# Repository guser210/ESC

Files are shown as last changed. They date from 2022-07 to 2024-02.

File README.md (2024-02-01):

# ESC

#ESC V2
https://github.com/guser210/ESC-V2

ESC - Electronic Speed Controller for BLDC Motors.

You can find more information on this link,
https://discord.gg/pByahDupYP

Component list: 

STM32G0 ARM Processor: Qty 1
https://www.mouser.com/ProductDetail/511-STM32G070KBT6

ADP Gate Driver: Qty 3
https://www.mouser.com/ProductDetail/863-ADP3120AJRZ-RL

Comparator: Qty 1
https://www.mouser.com/ProductDetail/511-LM339P

10v Regulator: Qty 1
https://www.mouser.com/ProductDetail/595-UA78L10ACLPRE3

3.3v Regulator: Qty 1
https://www.mouser.com/ProductDetail/595-LP2950-33LPRE3

Toshiba 30v 320A mosfet: Qty 6
https://www.mouser.com/ProductDetail/757-TPHR9203PL1LQ

1000uF Cap 100v: Qty 1
https://www.mouser.com/ProductDetail/80-ESK108M050AL4AA

4.7uF 100v ceramic capacitor: Qty 6
https://www.mouser.com/ProductDetail/81-GRM31CC72A475KE1K

1uf 100v ceramic capacitor: Qty 3
https://www.mouser.com/ProductDetail/963-HMR212CC7105KG-T

0.1uf 250v ceramic capacitor: Qty 1
https://www.mouser.com/ProductDetail/810-C2012X7T2E104MST

Switching diode 400v 3A: Qty 3
https://www.mouser.com/ProductDetail/241-GS1004FLR100001

Breakout boards:

LQFP-32 for ARM Processor: Qty 1
https://oshpark.com/shared_projects/X7qWhbM5

Mosfet driver: Qty 3
https://oshpark.com/shared_projects/A9uEdszS

Comparator LM339-TSSOP-14: Qty 1
https://oshpark.com/shared_projects/zJzdy7s3

Mosfet: Qty 3
https://oshpark.com/shared_projects/zwIIKerc

Flight Controller: Qty 1 Optional
https://www.getfpv.com/lumenier-lux-f7-ultimate-flight-controller-dual-gyros.html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 

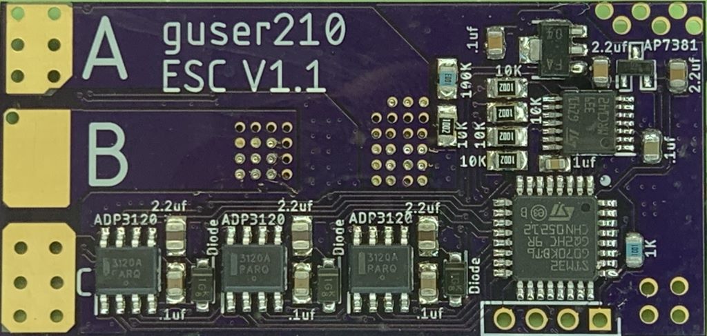
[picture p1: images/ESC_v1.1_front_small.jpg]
PCB Front test


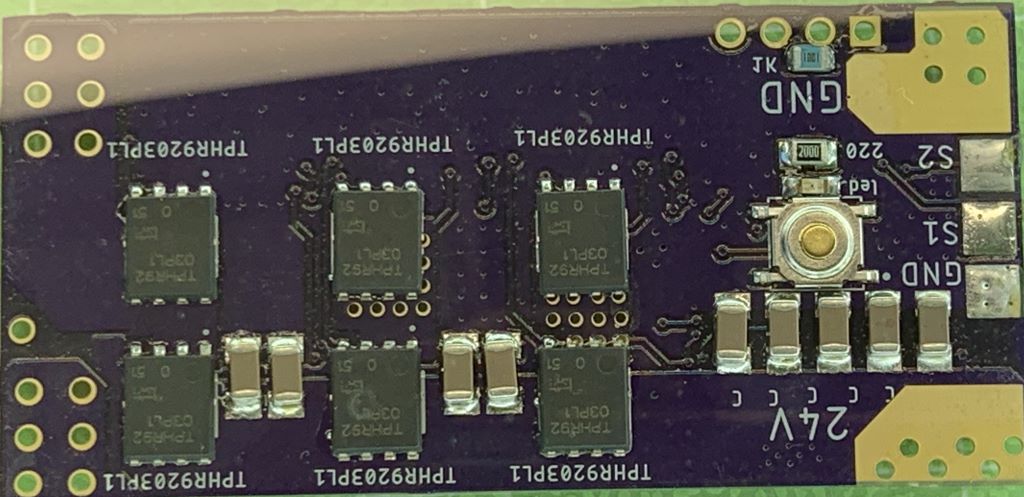
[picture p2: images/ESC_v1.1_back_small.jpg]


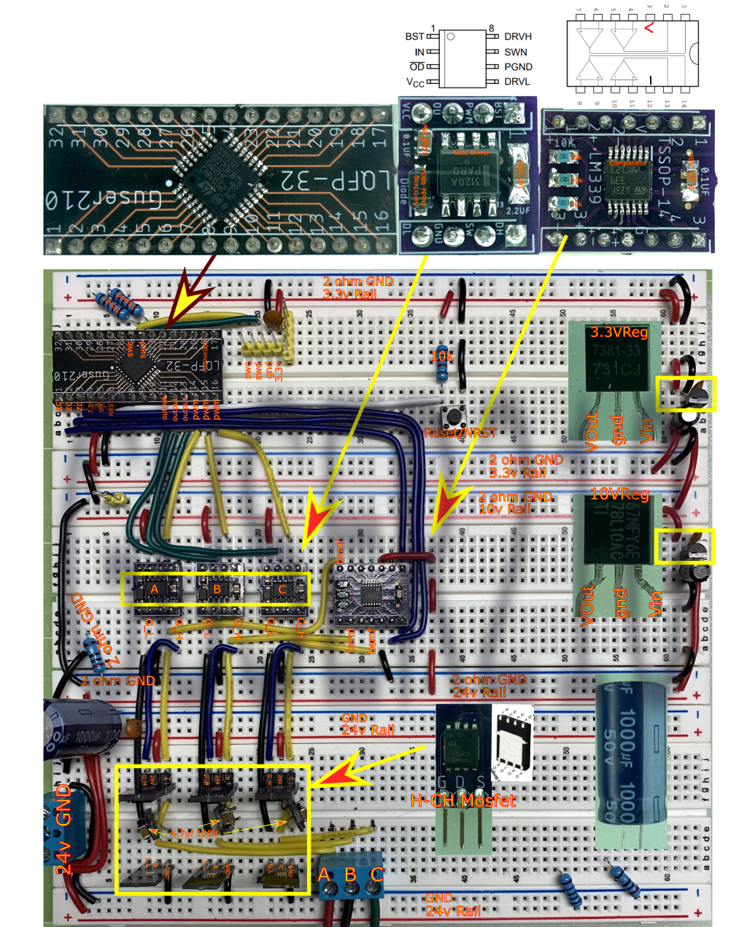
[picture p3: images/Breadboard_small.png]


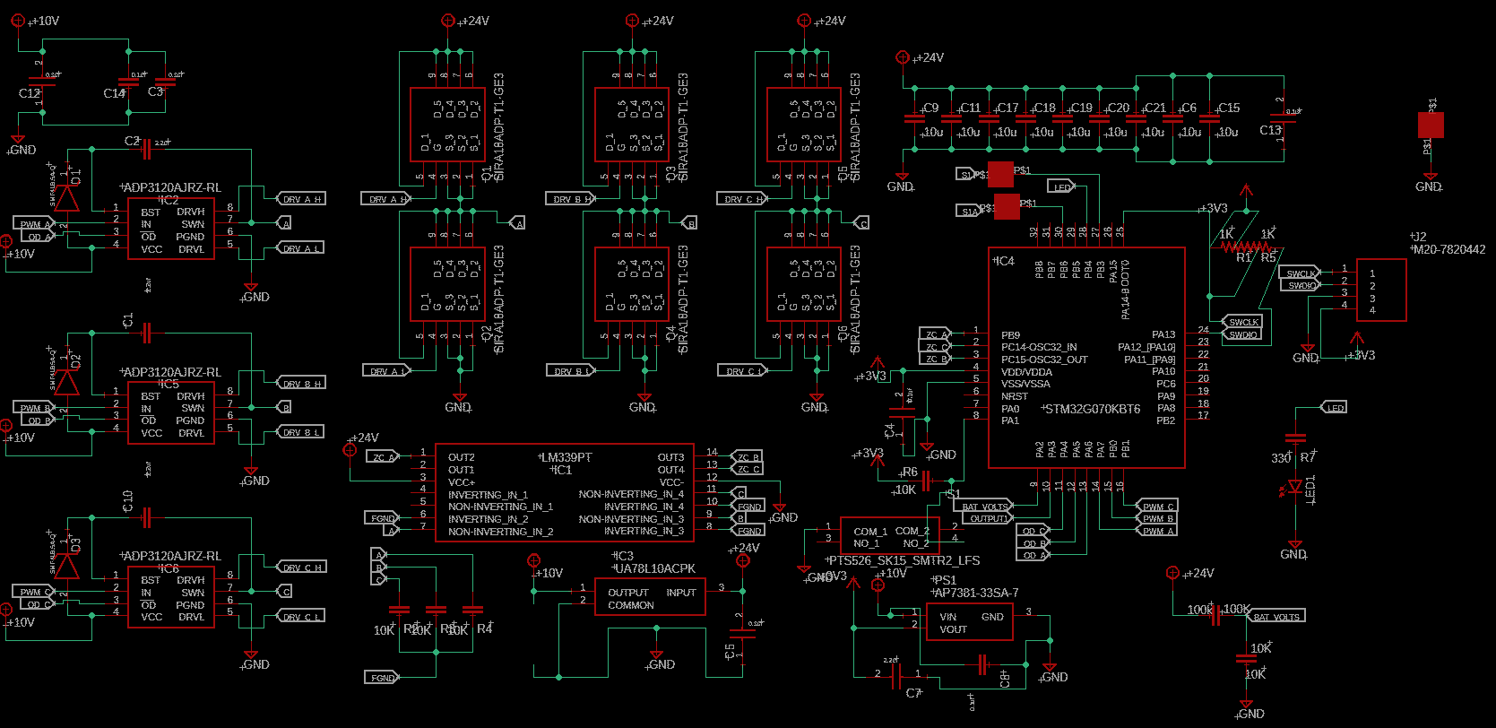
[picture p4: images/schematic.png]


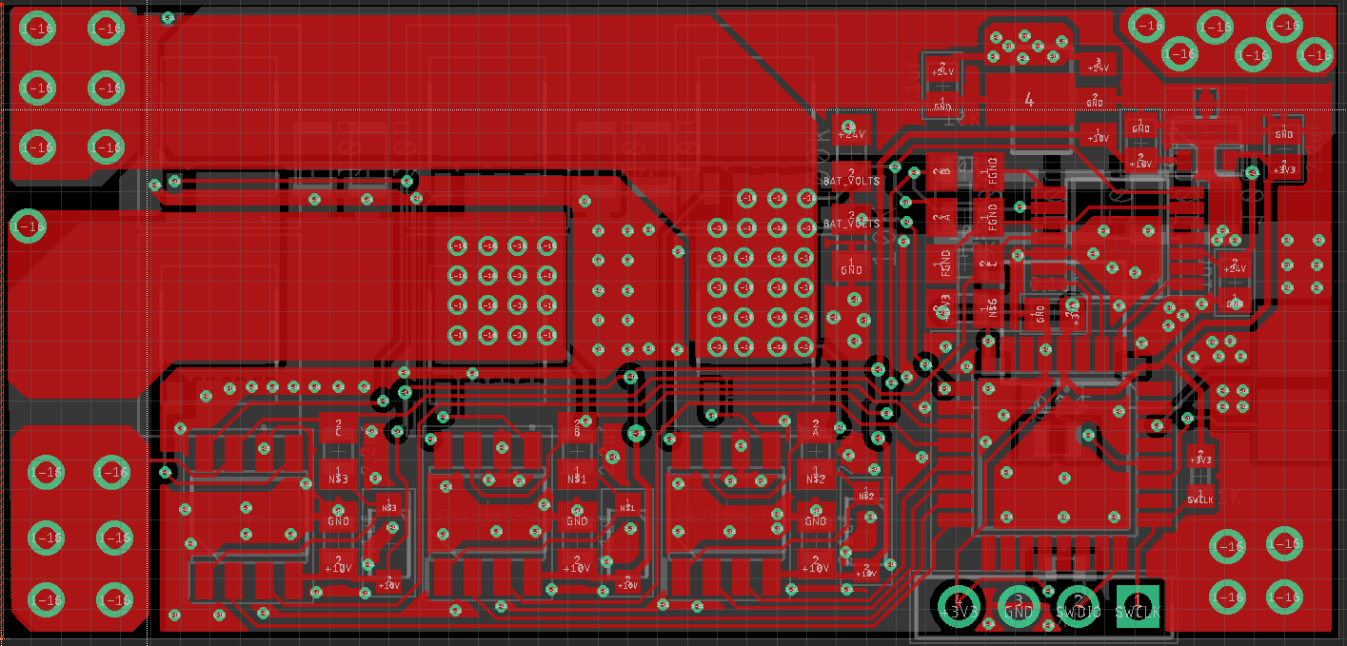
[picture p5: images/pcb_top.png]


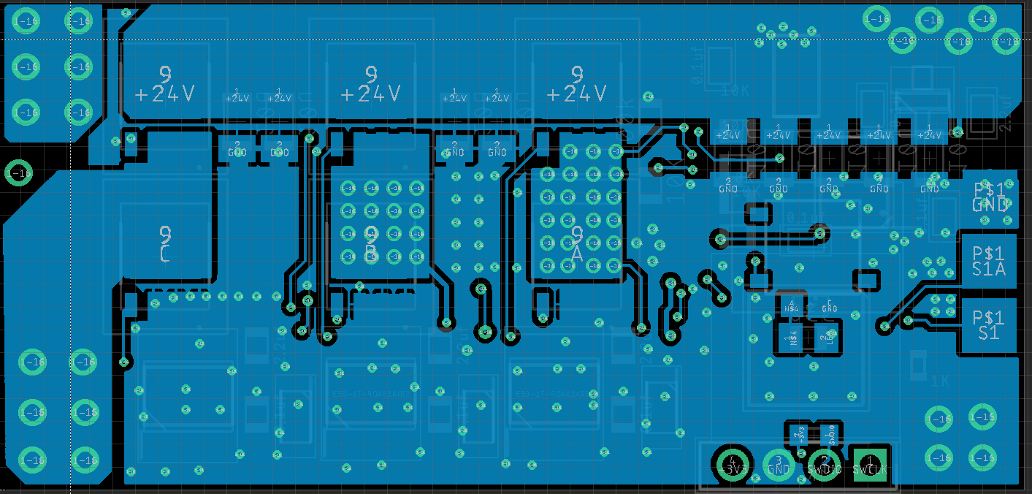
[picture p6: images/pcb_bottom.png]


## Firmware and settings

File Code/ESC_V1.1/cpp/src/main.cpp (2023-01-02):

/*
 * main.cpp
 *
 *  Created on: July 18, 2022
 *      Author: gvargas
 */

#include "main.h"

extern "C" {
extern TIM_HandleTypeDef htim1;		// Signal input capture.
extern TIM_HandleTypeDef htim3;		// PWM driver.
extern TIM_HandleTypeDef htim7;		// Generic timer.

extern TIM_HandleTypeDef htim6;		// RPM.

extern TIM_HandleTypeDef htim17;	// commutator bump timer.
extern ADC_HandleTypeDef hadc1;	// battery voltages.
}

volatile uint8_t newDmaSignal = 0;
volatile uint16_t dmaSignal[16] = { 0 };
volatile uint16_t dmaSignalNormalized[16] = { 0 };
volatile uint16_t motorSpeed = 0;
volatile uint16_t motorSpeedCurrent = 0;

//////////////////////////////////////////////////////////////////////
const uint16_t dmaPulse = 1;
const uint16_t dmaPulseReload = 1024;
volatile uint16_t dmaBuffer[dmaPulse] = { 0 };
volatile uint16_t resolution = dmaPulse * dmaPulseReload;
void setDutyCycle(uint16_t dc) {
	if (dc > resolution)
		dc = resolution;

	dmaBuffer[0] = dc;
	TIM3->CCR1 = dc;
}

const uint32_t zcOff[6] = {	//
		ZC_B_Pin, // B
				ZC_A_Pin, // A
				ZC_C_Pin, // C
				ZC_B_Pin, // B
				ZC_A_Pin, // A
				ZC_C_Pin, // C
		};

const uint32_t odLow[6] = { //
		OD_C_Pin, // C
				OD_C_Pin, // C
				OD_A_Pin, // A
				OD_A_Pin, // A
				OD_B_Pin, // B
				OD_B_Pin, // B
		};
const uint32_t odHigh[6] = { //
		OD_A_Pin, // A
				OD_B_Pin, // B
				OD_B_Pin, // B
				OD_C_Pin, // C
				OD_C_Pin, // C
				OD_A_Pin, // A
		};

const uint32_t odOff[6] = { //
		OD_B_Pin, // B
				OD_A_Pin, // A
				OD_C_Pin, // C
				OD_B_Pin, // B
				OD_A_Pin, // A
				OD_C_Pin, // C
		};

const uint32_t ccOff[6] = { // TIME3->CCER For pwm output, RM0454 page 495.
		1 << 8, // B
		1 << 4, // A
		1 << 12, // C
		1 << 8, // B
		1 << 4, // A
		1 << 12, // C
		};

const uint32_t diOff[6] = { // TIM3->DIER for PWM output RM0454 page .
		1 << 11, // B
		1 << 10, // A
		1 << 12, // C
		1 << 11, // B
		1 << 10, // A
		1 << 12, // C
		};

const GPIO_TypeDef *zcPortOff[6] = { //
		(GPIO_TypeDef*) ZC_B_GPIO_Port, // B
				(GPIO_TypeDef*) ZC_A_GPIO_Port, // A
				(GPIO_TypeDef*) ZC_C_GPIO_Port, // C
				(GPIO_TypeDef*) ZC_B_GPIO_Port, // B
				(GPIO_TypeDef*) ZC_A_GPIO_Port, // A
				(GPIO_TypeDef*) ZC_C_GPIO_Port, // C
		};
volatile uint32_t resetImrFlags = 0;
volatile uint8_t powerStep = 0;
volatile uint8_t powerStepCurrent = 0;

const uint8_t rising[2][6] = { { 1, 0, 1, 0, 1, 0 }, { 0, 1, 0, 1, 0, 1 } };

volatile uint8_t reverse = 0;

#define zcPinOn ZC_A_Pin | ZC_B_Pin | ZC_C_Pin
volatile uint16_t commutationCNT = 0;

inline void commutate() {
	commutationCNT = TIM6->CNT;
	TIM6->CNT = 0;
	// go to next power step.
	powerStepCurrent++;
	powerStepCurrent %= 6;

	if (reverse)
		powerStep = 5 - powerStepCurrent;
	else
		powerStep = powerStepCurrent; // forward.

	if (rising[reverse][powerStep]) {
		// if zc rising
		//		enable zc rising interrupt
		EXTI->FTSR1 = 0;
		EXTI->RTSR1 = zcOff[powerStep];
		//		enable odLow
		GPIOA->BSRR = odLow[powerStep];
		GPIOA->BRR = odOff[powerStep]; // disable odOff

		TIM3->CCER |= (ccOff[powerStep]);
		//		enable dma on timer 3.
		TIM3->DIER |= (diOff[powerStep]);
	} else {
		// else
		//		enable zc falling int.
		EXTI->RTSR1 = 0;
		EXTI->FTSR1 = zcOff[powerStep];
		//		enable odHigh.
		GPIOA->BRR = odOff[powerStep]; // disable odOff
		GPIOA->BSRR = odHigh[powerStep];

		TIM3->CCER &= ~(ccOff[powerStep]);
		//		disable dma on timer 3
		TIM3->DIER &= ~(diOff[powerStep]);

	}

	// enable wakeup with interrupt.
	EXTI->IMR1 = resetImrFlags | zcOff[powerStep];
	// clear any zc pending interrupts.
	EXTI->FPR1 = zcPinOn;
	EXTI->RPR1 = zcPinOn;

	// reset timer17 for bump motor.
	TIM17->CNT = 0;
}

volatile uint16_t checkRising = 0;
volatile uint16_t checkFalling = 0;
void HAL_GPIO_EXTI_Rising_Callback(uint16_t GPIO_Pin) {

	TIM7->CNT = 0;
	while ( TIM7->CNT < checkRising)
		if ((zcPortOff[powerStep]->IDR & zcOff[powerStep]) == 0) {
			return;
		}

	commutate();
}
void HAL_GPIO_EXTI_Falling_Callback(uint16_t GPIO_Pin) {

	TIM7->CNT = 0;

	while ( TIM7->CNT < checkFalling)
		if ((zcPortOff[powerStep]->IDR & zcOff[powerStep])) {
			return;
		}

	commutate();
}

void HAL_TIM_PeriodElapsedCallback(TIM_HandleTypeDef *htim) {
	if (htim == &htim17) {
//		if( reverse == 0)
//			HAL_GPIO_TogglePin(LED_GPIO_Port, LED_Pin);
		if (motorSpeedCurrent > 0) { // Bump
			HAL_GPIO_TogglePin(LED_GPIO_Port, LED_Pin);
			commutate();
		}
	}

}
void HAL_TIM_OC_DelayElapsedCallback(TIM_HandleTypeDef *htim) {
	if (htim == &htim17 && htim->Channel == HAL_TIM_ACTIVE_CHANNEL_1) {
		if (motorSpeedCurrent > 0) { // Bump
			HAL_GPIO_TogglePin(LED_GPIO_Port, LED_Pin);
			commutate();
		}
	}
}

//////////////////////////////////////////////////////////////////////

uint16_t divClosest(uint16_t a, uint16_t b) {
	return (a + b / 2) / b;
}

volatile uint8_t frequencyType = 0; // 0 = Proshot, 1=PWM.
volatile uint16_t pwm[3] = { 0 };
volatile uint8_t transmitterDirection = 0;
volatile uint8_t masterDirection = 0;
volatile uint16_t pwm1 = 0;
volatile uint16_t pwm2 = 0;

volatile uint8_t directionValidator = 0;
void processDmaSignalPWM() {
	newDmaSignal = 0;

	pwm1 = divClosest(dmaSignal[2] - dmaSignal[1], 4);
	pwm2 = divClosest(dmaSignal[1] - dmaSignal[0], 4);

	pwm[0] = pwm1;
	pwm[1] = pwm2;
	pwm[2] = divClosest(pwm1 + pwm2, 1000);

	if (pwm[2] == 7) {
		directionValidator--;
		if (directionValidator < 1) {
			directionValidator = 1;
			transmitterDirection = masterDirection;
		}

	} else if (pwm[2] == 8) {
		directionValidator++;
		if (directionValidator > 10) {
			directionValidator = 10;
			if (masterDirection == 0)
				transmitterDirection = 1;
			else
				transmitterDirection = 0;
		}
	}

	pwm1 = pwm1 < pwm2 ? pwm1 : pwm2;

	motorSpeed = pwm1 > 1001 && pwm1 < 2010 ? (pwm1 + 24) - 1000 : 0;

}

void processDmaSignal() {
	newDmaSignal = 0;

	for (int index = 0; index < 15; index++)
		dmaSignalNormalized[index] = divClosest(
				dmaSignal[index + 1] - dmaSignal[index], 8) - 8;

//
	if (dmaSignalNormalized[0] > 1000 && dmaSignalNormalized[1] > 1000
			&& dmaSignalNormalized[2] > 1000) {
		return;
	}

	for (int index = 0; index <= 10; index++) {
		if (dmaSignalNormalized[index] < 100)
			continue;
		if (dmaSignalNormalized[index + 1] > 3000)
			continue;

		uint16_t motorSpeedNewValue = dmaSignalNormalized[index + 1] << 6
				| dmaSignalNormalized[index + 3] << 2
				| dmaSignalNormalized[index + 5] >> 2;
		if (motorSpeedNewValue < 1026)
			motorSpeed = motorSpeedNewValue;

		break;
	}

}

void HAL_TIM_IC_CaptureCallback(TIM_HandleTypeDef *htim) {
	if (htim == &htim1 && htim->Channel == HAL_TIM_ACTIVE_CHANNEL_3)
		newDmaSignal = 1;
}

inline uint16_t map(int x, int in_min, int in_max, int out_min, int out_max) {
	if (x < in_min)
		x = in_min;

	if (x > in_max)
		x = in_max;

	return (x - in_min) * (out_max - out_min) / (in_max - in_min) + out_min;
}

volatile double batteryVoltages = 0.0f;
volatile double adcValue = 0;
volatile uint16_t fallingPaddingValue = 0;

uint8_t memorySettings[32] = { 0 };
int sizeOfSettings = sizeof(memorySettings);
void readMemory(unsigned char *data, int size, int location) {
	location *= 8;

	for (int index = 0; index < size; index++) {
		data[index] = (unsigned int) (*(uint64_t*) (0x0801F800 + location));
		location += 8;
	}

}

void writeMemory(unsigned char *data, int size, int location) {

	readMemory(memorySettings, sizeOfSettings, 0);

	size = size > sizeOfSettings ? sizeOfSettings : size;
	location = location >= sizeOfSettings ? sizeOfSettings : location;

	for (int index = 0; index < size; index++) {
		location = location >= sizeOfSettings ? sizeOfSettings : location;
		memorySettings[location++] = data[index];
	}

	FLASH_EraseInitTypeDef epage;
	epage.TypeErase = FLASH_TYPEERASE_PAGES; // FLASH_TYPEERASE_PAGES
	epage.Page = 63;
	epage.NbPages = 1;

	uint32_t error = 0;
//	HAL_StatusTypeDef ret =
	HAL_FLASH_Unlock();

//	ret =
	HAL_FLASHEx_Erase(&epage, &error);
	for (int index = 0; index < sizeOfSettings; index++) {
		//ret =
		HAL_FLASH_Program(FLASH_TYPEPROGRAM_DOUBLEWORD,
				0x0801F800 + (index * 8), memorySettings[index]);
	}

	//ret =
	HAL_FLASH_Unlock();

}

volatile uint16_t frequencyProbability[2] = { 0, 0 };
volatile uint16_t signalValue[4] = { 0 };
void detechFrequency() {

	signalValue[0] = divClosest(dmaSignal[1] - dmaSignal[0], 8);
	signalValue[1] = divClosest(dmaSignal[3] - dmaSignal[2], 8);
	if (signalValue[0] >= 100 && signalValue[0] < 200 && signalValue[1] > 0
			&& signalValue[1] < 5)
		frequencyProbability[0] += 1;

	if (signalValue[0] > 500 && signalValue[1] > 500)
		frequencyProbability[1] += 1;

}
void setup() {

	EXTI->FTSR1 = 0;
	EXTI->RTSR1 = 0;
	HAL_Delay(1000);
	resetImrFlags = EXTI->IMR1;
	resetImrFlags &= ~(ZC_A_Pin | ZC_B_Pin | ZC_C_Pin);
	EXTI->IMR1 = resetImrFlags;

	HAL_TIM_IC_Start_DMA(&htim1, TIM_CHANNEL_3, (uint32_t*) dmaSignal, 16);

	if (HAL_TIM_Base_Start(&htim3) != HAL_OK)
		Error_Handler();

	TIM3->CCR2 = 0;
	TIM3->CCR3 = 0;
	TIM3->CCR4 = 0;
	HAL_TIM_PWM_Start(&htim3, TIM_CHANNEL_2);
	HAL_TIM_PWM_Start(&htim3, TIM_CHANNEL_3);
	HAL_TIM_PWM_Start(&htim3, TIM_CHANNEL_4);

	HAL_TIM_PWM_Stop_DMA(&htim3, TIM_CHANNEL_2);
	HAL_TIM_PWM_Stop_DMA(&htim3, TIM_CHANNEL_3);
	HAL_TIM_PWM_Stop_DMA(&htim3, TIM_CHANNEL_4);

	HAL_TIM_PWM_Start_DMA(&htim3, TIM_CHANNEL_2, (uint32_t*) dmaBuffer,
			dmaPulse);
	HAL_TIM_PWM_Start_DMA(&htim3, TIM_CHANNEL_3, (uint32_t*) dmaBuffer,
			dmaPulse);
	HAL_TIM_PWM_Start_DMA(&htim3, TIM_CHANNEL_4, (uint32_t*) dmaBuffer,
			dmaPulse);

	__HAL_TIM_SET_COMPARE(&htim17, TIM_CHANNEL_1, 250);
	HAL_TIM_OC_Start_IT(&htim17, TIM_CHANNEL_1);
	HAL_Delay(100);


}

volatile int motorSpeedDirection = 1;
volatile uint8_t direction = 0;
volatile uint32_t eRPM = 0;
void maincpp() {
	HAL_NVIC_DisableIRQ(EXTI4_15_IRQn);
	for (int i = 0; i < 10; i++) {
		HAL_GPIO_TogglePin(LED_GPIO_Port, LED_Pin);
		HAL_Delay(100);
	}

	HAL_ADCEx_Calibration_Start(&hadc1);
	HAL_ADC_Start(&hadc1);
	if (HAL_TIM_Base_Start(&htim7) != HAL_OK)
		Error_Handler();

	if (HAL_TIM_Base_Start(&htim6) != HAL_OK) // RPM
		Error_Handler();

	setup();

	for (int index = 0; index < 100; index++) {
		/*
		 * check input signal 100 times
		 * detect signal type (PWM/Proshot1000) before start.
		 */
		__HAL_TIM_SET_COUNTER(&htim1, 0);
		__HAL_TIM_SET_PRESCALER(&htim1, 8);

		HAL_TIM_IC_Start_DMA(&htim1, TIM_CHANNEL_3, (uint32_t*) dmaSignal, 4);
		HAL_Delay(10);
		if (newDmaSignal) {
			detechFrequency();
		}
		HAL_GPIO_TogglePin(LED_GPIO_Port, LED_Pin);

	}

	if (frequencyProbability[0] > frequencyProbability[1]) {
		frequencyType = 0;
		/*
		 * change prescale and let it overflow for the change to take effect.
		 */
		__HAL_TIM_SET_COUNTER(&htim1, 0);
		__HAL_TIM_SET_PRESCALER(&htim1, 0);
		HAL_Delay(1000); // overflow timer.

		HAL_TIM_IC_Start_DMA(&htim1, TIM_CHANNEL_3, (uint32_t*) dmaSignal, 16);
	} else {

		frequencyType = 1;
		/*
		 * change prescale and let it overflow for the change to take effect.
		 */
		__HAL_TIM_SET_COUNTER(&htim1, 0);
		__HAL_TIM_SET_PRESCALER(&htim1, 16 - 1);
		HAL_Delay(1000); // overflow timer.

		HAL_TIM_IC_Start_DMA(&htim1, TIM_CHANNEL_3, (uint32_t*) dmaSignal, 3);

	}

	uint8_t memorySetting[1] = { 0 };

	readMemory(memorySettings, sizeOfSettings, 0);
	if (memorySettings[0] != 1)
		memorySettings[0] = 0;

	masterDirection = memorySetting[0];
	direction = masterDirection;
	reverse = masterDirection;

	uint8_t testMotor = 0;
	uint8_t motorSpinning = 0;
	while (1) {

		eRPM = (((1000000 / (commutationCNT / 32)) * 60) / 7); ///6; /6 will give you RPM
		uint8_t testCounter = 0;

		if ((REV_GPIO_Port->IDR & REV_Pin) == 0) { // switch direction when button pressed.

			LED_GPIO_Port->BSRR = LED_Pin;
			HAL_Delay(500);
			LED_GPIO_Port->BRR = LED_Pin;

			if (masterDirection == 1)
				direction = 0;
			else
				direction = 1;

			memorySetting[0] = direction;
			masterDirection = direction;
			writeMemory(memorySetting, 1, 0);

			if (testMotor) {
				motorSpeed = 0;
				motorSpeedCurrent = 0;
				setDutyCycle(0);
			}
			testCounter = 0;
			testMotor = 0;

			while ((REV_GPIO_Port->IDR & REV_Pin) == 0) {

				if (testCounter++ > 30) {

					testMotor = 1;
					while ((REV_GPIO_Port->IDR & REV_Pin) == 0) {
						HAL_Delay(50);
						HAL_GPIO_TogglePin(LED_GPIO_Port, LED_Pin);
					}
				}

				HAL_Delay(50);
			}
			LED_GPIO_Port->BRR = LED_Pin;
		}

		if (reverse == 1)
			LED_GPIO_Port->BSRR = LED_Pin;
		else
			LED_GPIO_Port->BRR = LED_Pin;

		if (newDmaSignal || testMotor) {
			if (!testMotor) {
				if (frequencyType == 0) {
					processDmaSignal();
				} else {
					processDmaSignalPWM();
					if (transmitterDirection != direction)
						direction = transmitterDirection;
				}
			} else {
				motorSpeed += motorSpeedDirection;
				HAL_Delay(30);

				if (motorSpeed > 300 || motorSpeed <= 0) {

					motorSpeedDirection *= -1;
					if (motorSpeedDirection == 1) {
						if (direction == 1)
							direction = 0;
						else
							direction = 1;
					}
				}

			}

			if (direction != reverse) {
				motorSpeedCurrent = 0;
				setDutyCycle(motorSpeedCurrent);
				reverse = direction;
				HAL_Delay(100);
			}

			adcValue = HAL_ADC_GetValue(&hadc1);

			if (adcValue > 0) {
				//											rb/rt
				batteryVoltages = adcValue * (3.3 / 4095.0)
						/ (10000.0 / 110000.0);

				fallingPaddingValue = map(batteryVoltages, 8, 25, 1, 400);
			}

			if (motorSpeed != motorSpeedCurrent) {
				if (motorSpeedCurrent > 200 && eRPM < 5000) { // TODO: add proper calculation to RPM.
					motorSpeedCurrent = 0;
					setDutyCycle(motorSpeedCurrent);
					HAL_Delay(20);

				}
				if (motorSpeedCurrent == 0)
					commutate();
				if (motorSpeedCurrent < 100) {
					if ((motorSpeed - motorSpeedCurrent) > 10)
						motorSpeedCurrent += 10;
					else
						motorSpeedCurrent = motorSpeed;

				} else {
					if ((motorSpeed - motorSpeedCurrent) > 50)
						motorSpeedCurrent += 50;
					else
						motorSpeedCurrent = motorSpeed;
				}

				if (motorSpeedCurrent < 150) {
					checkRising = 1400
							- map(batteryVoltages, 8, 21, 1,
									map(motorSpeedCurrent, 1, 200, 2, 1400)

											);
				} else {
					checkRising = map(1024 - motorSpeedCurrent, 0, 1024, 1,
							320);
				}
				checkFalling = map(1024 - motorSpeedCurrent, 0, 1024, 1, 900);

				if (motorSpeedCurrent == 0 && motorSpinning) { // allows to remove motor spinning check on interrupt, prevents volt spikes on cutoff
					motorSpinning = 0;
					HAL_NVIC_DisableIRQ(EXTI4_15_IRQn);
				} else if (motorSpeedCurrent > 0 && !motorSpinning) {
					motorSpinning = 1;
					HAL_NVIC_SetPriority(EXTI4_15_IRQn, 0, 0);
					HAL_NVIC_EnableIRQ(EXTI4_15_IRQn);

				}
				setDutyCycle(motorSpeedCurrent);

			}

			if (frequencyType == 1) // PWM
					{
				TIM1->CNT = 0;
				HAL_TIM_IC_Start_DMA(&htim1, TIM_CHANNEL_3,
						(uint32_t*) dmaSignal, 3);
			} else {
				TIM1->CNT = 0;
				HAL_TIM_IC_Start_DMA(&htim1, TIM_CHANNEL_3,
						(uint32_t*) dmaSignal, 16);
			}

		}

	}
}

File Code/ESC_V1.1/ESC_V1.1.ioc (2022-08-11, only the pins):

Mcu.UserName=STM32G070KBTx
PA1.GPIO_Label=REV
PA1.Signal=GPIO_Input
PA13.Signal=SYS_SWDIO
PA14-BOOT0.Signal=SYS_SWCLK
PA2.GPIO_Label=BAT_VOLTS
PA2.Signal=ADC1_IN2
PA4.GPIO_Label=OD_C
PA4.Signal=GPIO_Output
PA5.GPIO_Label=OD_B
PA5.Signal=GPIO_Output
PA6.GPIO_Label=OD_A
PA6.Signal=GPIO_Output
PA7.GPIO_Label=PWM_A
PA7.Signal=S_TIM3_CH2
PB0.GPIO_Label=PWM_B
PB0.Signal=S_TIM3_CH3
PB1.GPIO_Label=PWM_C
PB1.Signal=S_TIM3_CH4
PB3.GPIO_Label=Signal
PB3.Signal=S_TIM1_CH2
PB4.GPIO_Label=LED
PB4.Signal=GPIO_Output
PB6.GPIO_Label=Proshot
PB6.Signal=S_TIM1_CH3
PB9.GPIO_Label=ZC_A
PB9.Signal=GPXTI9

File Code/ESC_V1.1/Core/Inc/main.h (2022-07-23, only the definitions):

#define ZC_A_Pin GPIO_PIN_9
#define ZC_A_GPIO_Port GPIOB
#define ZC_A_EXTI_IRQn EXTI4_15_IRQn
#define ZC_C_Pin GPIO_PIN_14
#define ZC_C_GPIO_Port GPIOC
#define ZC_C_EXTI_IRQn EXTI4_15_IRQn
#define ZC_B_Pin GPIO_PIN_15
#define ZC_B_GPIO_Port GPIOC
#define ZC_B_EXTI_IRQn EXTI4_15_IRQn
#define REV_Pin GPIO_PIN_1
#define REV_GPIO_Port GPIOA
#define BAT_VOLTS_Pin GPIO_PIN_2
#define BAT_VOLTS_GPIO_Port GPIOA
#define OD_C_Pin GPIO_PIN_4
#define OD_C_GPIO_Port GPIOA
#define OD_B_Pin GPIO_PIN_5
#define OD_B_GPIO_Port GPIOA
#define OD_A_Pin GPIO_PIN_6
#define OD_A_GPIO_Port GPIOA
#define PWM_A_Pin GPIO_PIN_7
#define PWM_A_GPIO_Port GPIOA
#define PWM_B_Pin GPIO_PIN_0
#define PWM_B_GPIO_Port GPIOB
#define PWM_C_Pin GPIO_PIN_1
#define PWM_C_GPIO_Port GPIOB
#define Signal_Pin GPIO_PIN_3
#define Signal_GPIO_Port GPIOB
#define LED_Pin GPIO_PIN_4
#define LED_GPIO_Port GPIOB
#define Proshot_Pin GPIO_PIN_6
#define Proshot_GPIO_Port GPIOB

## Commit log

2022-07-23 Version 1.1
    [copper_bottom.gbr, copper_top.gbr, drill_1_16.xln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]
2022-08-02 Fix Switch from proshot and pwm
    [ESC_V1.1.ioc, main.cpp]

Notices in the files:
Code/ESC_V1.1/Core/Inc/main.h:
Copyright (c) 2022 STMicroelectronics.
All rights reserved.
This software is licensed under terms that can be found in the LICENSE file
